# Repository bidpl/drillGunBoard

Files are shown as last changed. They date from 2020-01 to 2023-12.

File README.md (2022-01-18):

# 12V Motor Testing Rig

Code for FRC control board. Manual control FRC motors and air compressor.

We used 12v drills to power 12v FRC motors, (CIMs, BAGs, etc) by removing drill spindle and connecting to motor leads. However, it can not supply large amounts of power. It can not drive Neo motors due to their brushless nature. 

This code is for a meant for a test rig that take a pot input and controls PWM motor controlers (Talon SRXs and Spark Maxes are used in this build).

Features:
Control multiple motors (up to 4) (Control moudes v1.1 and v1.2 have support for 5)
LCD readout for motor power

Documentation is a bit scuffed, I only used the repo while developing the first version (v1.0), didn't for later iterations (v1.1/1.2)

v1.0 was based on an arduino uno with regular potentiometers. The arduino by itself was limited to Talon SRXs since it could not generate a stable enough PWM signal for the Spark Max. This version used regular pin headers and cheap dupont wires so it suffered some durability issues (connections were terrible, shaking the testing rig could disconnect parts).

v1.1/1.2 is uses a custom control module (based on an ATMEGA32P, programs exactly like an UNO) that has an additional PWM driver chip (PCA9685). This chip can generate a proper 50hz PWM signal so it can control Spark Maxes as well. This version also uses locking connectors (JST-XH between input modules and the control module, Molex SL connectors for control module to motor controllers).

## PCB Modules
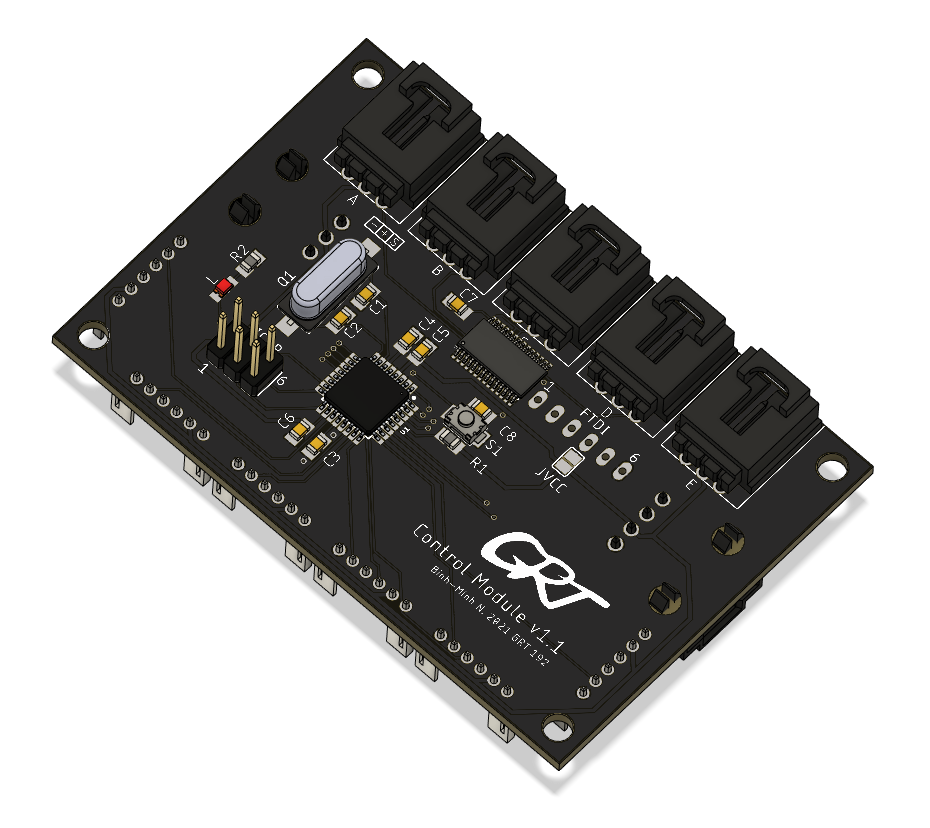
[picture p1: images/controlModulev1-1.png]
Control Module v1.1/v1.2

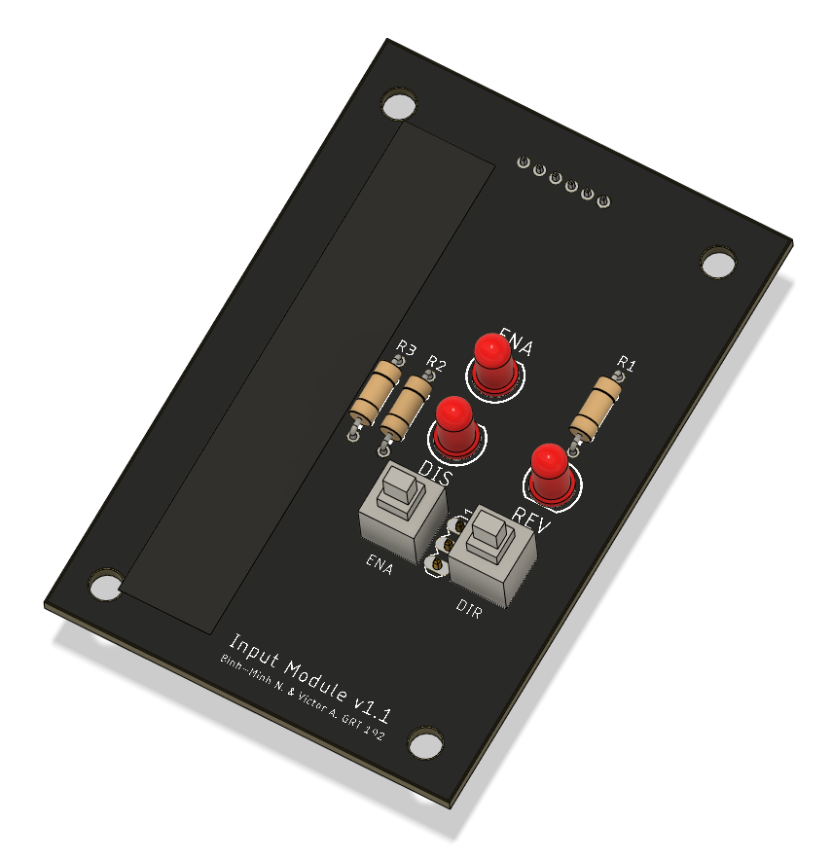
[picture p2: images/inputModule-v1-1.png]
Input Module v1.1


## Testing Rig (The Bomb, name inspired from Die Hard with a Vengeance)
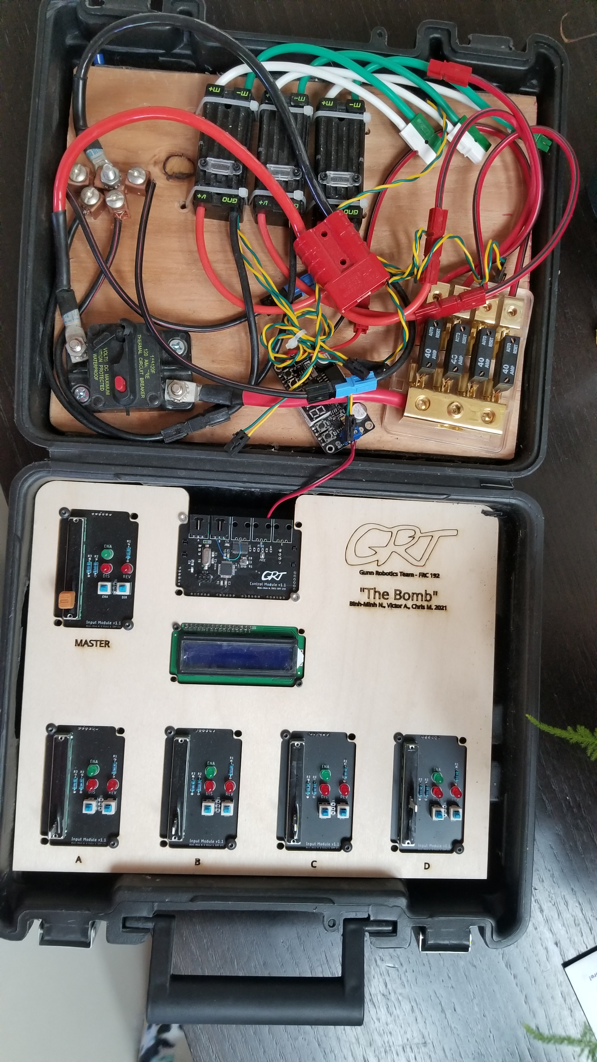
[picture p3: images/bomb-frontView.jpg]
Testing Rig Front View

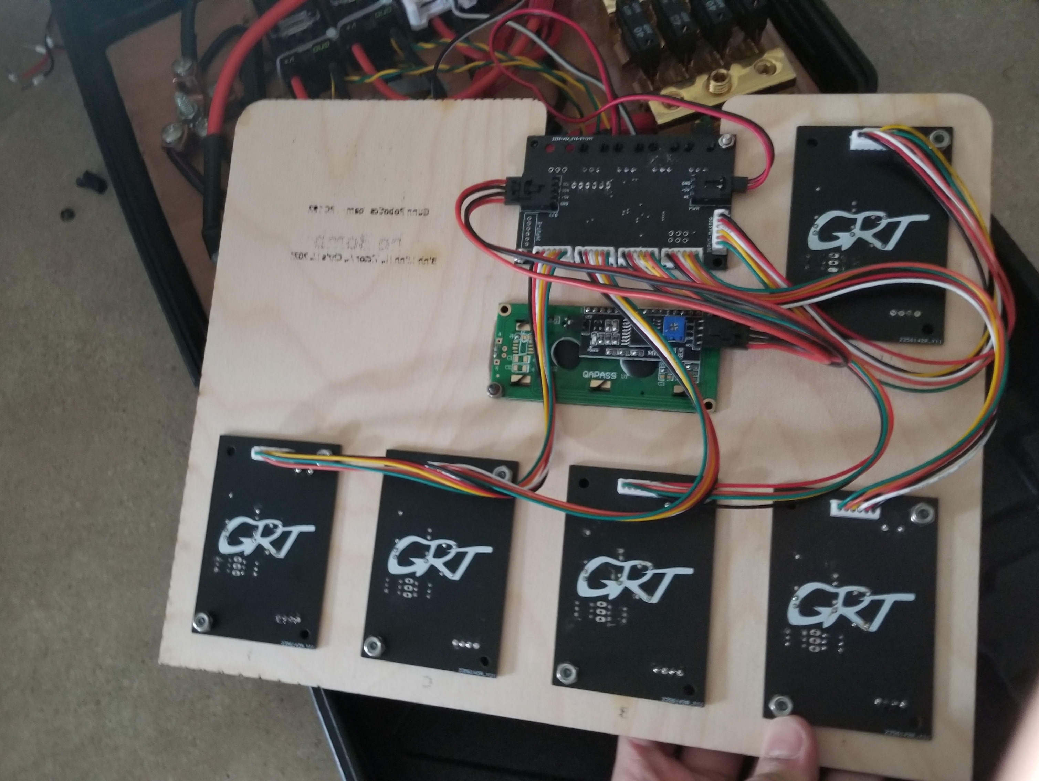
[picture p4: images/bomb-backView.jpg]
Testing Rig Back View


## Change Log
Input Module v1.1:
- Switched from rotate to linear potentiometer
- Switched from horizontal to vertical PCB shape

Control Module v1.2:
- Fixed PCA9685 CE signal (supposed to be active low, was tied high in prev version)

Control Module v1.1:
- Moved from arduino to custom PCB
- Added PCA9685 as PWM signal generator, arduino couldn't get a clean enough PWM signal for some motor controllers (Controlling the LCD delayed the signal too much)
- Switched from loose dupont wire to locking Molex-SL and JST-XH connectors

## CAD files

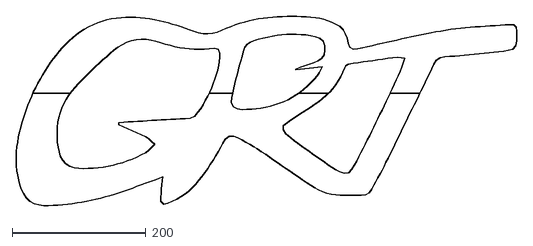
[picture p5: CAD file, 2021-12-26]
pcbs/motorTesting Rig/GRTlogo.dxf
749.8 x 283.4

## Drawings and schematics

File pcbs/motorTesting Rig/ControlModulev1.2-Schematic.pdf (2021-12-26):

# GND VCC 10k

# GND VCC

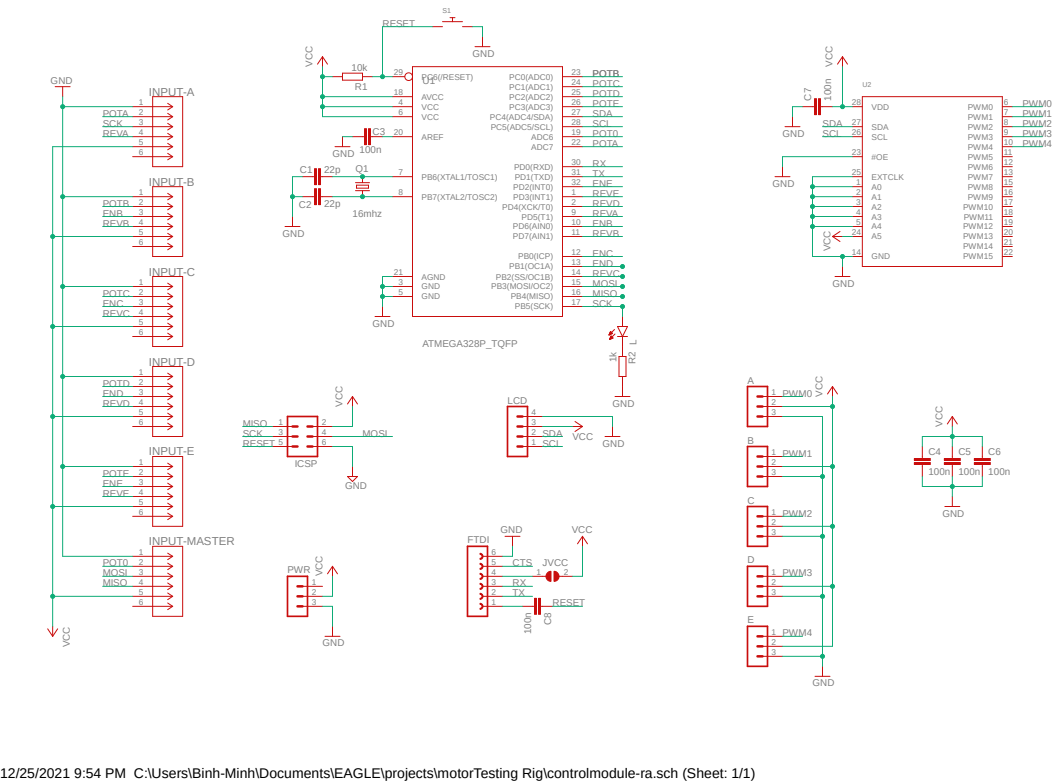
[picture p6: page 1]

12/25/2021 9:54 PM C:\Users\Binh-Minh\Documents\EAGLE\projects\motorTesting Rig\controlmodule-ra.sch (Sheet: 1/1)

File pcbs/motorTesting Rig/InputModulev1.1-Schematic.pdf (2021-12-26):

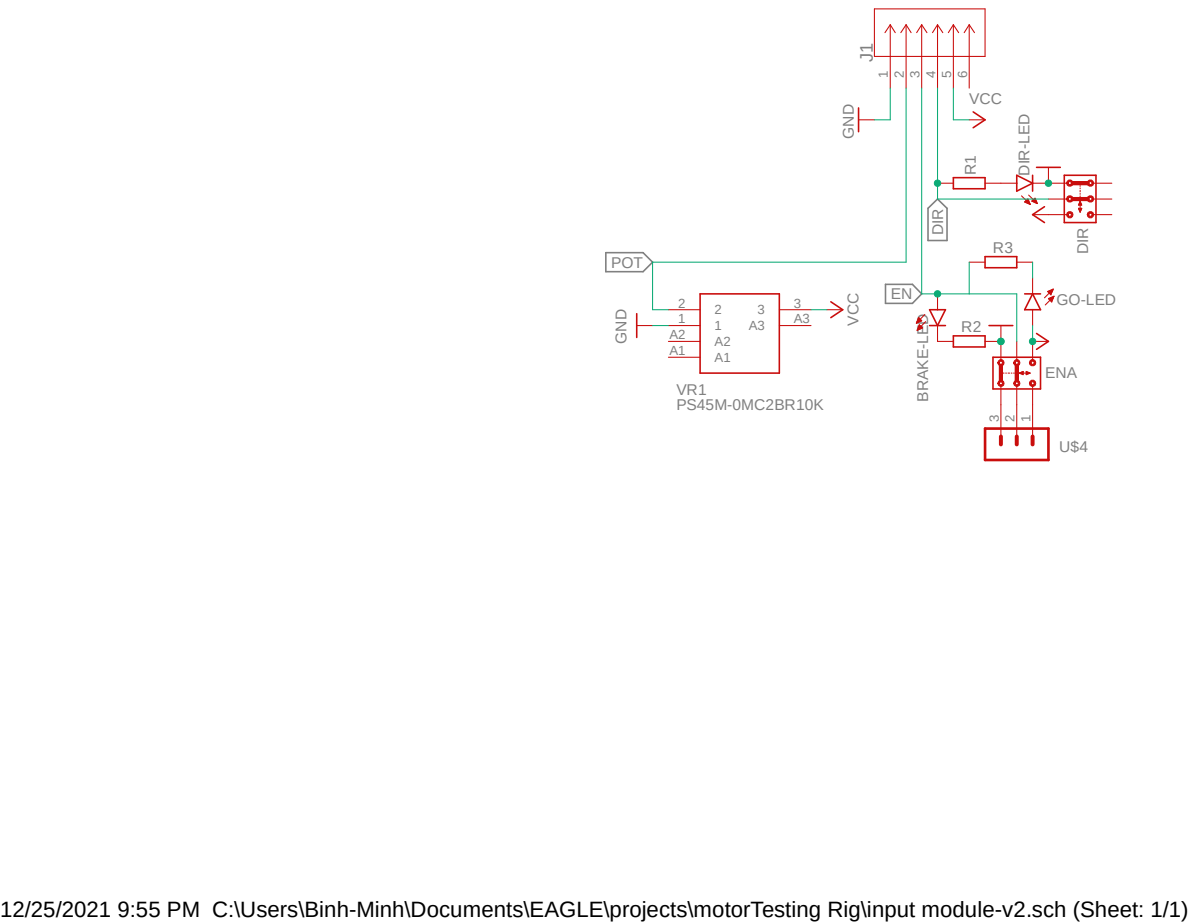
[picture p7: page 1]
12/25/2021 9:55 PM C:\Users\Binh-Minh\Documents\EAGLE\projects\motorTesting Rig\input module-v2.sch (Sheet: 1/1) VCC GND; GND; VCC; ENA DIR BRAKE⁻LED; DIR⁻LED; POT; DIR

GO-LED R¹

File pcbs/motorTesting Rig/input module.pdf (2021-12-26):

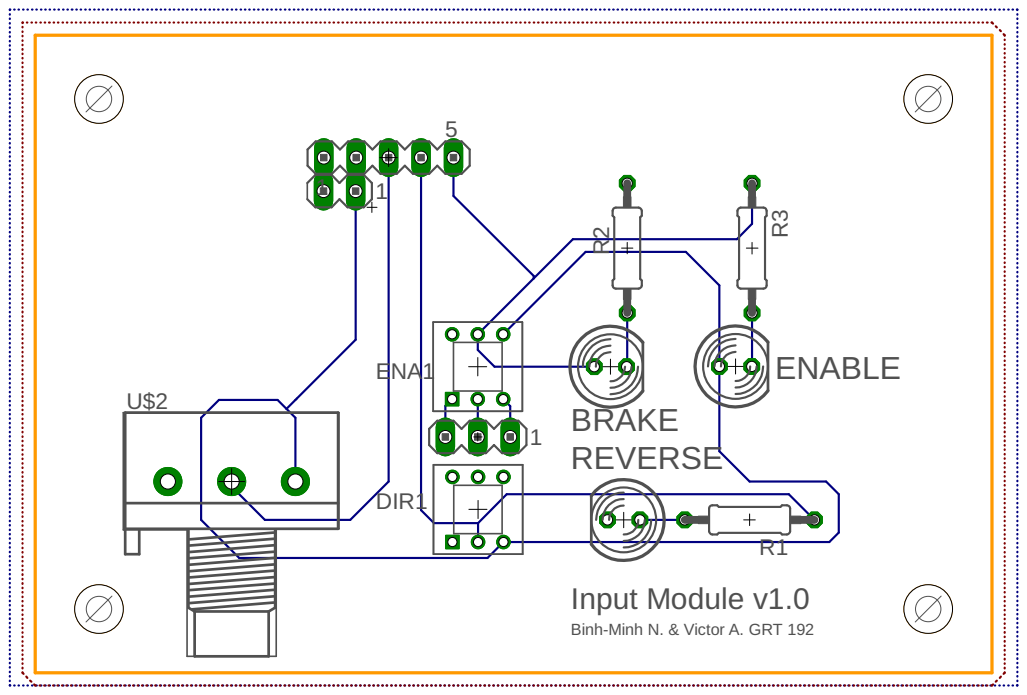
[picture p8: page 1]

Binh-Minh N. & Victor A. GRT 192

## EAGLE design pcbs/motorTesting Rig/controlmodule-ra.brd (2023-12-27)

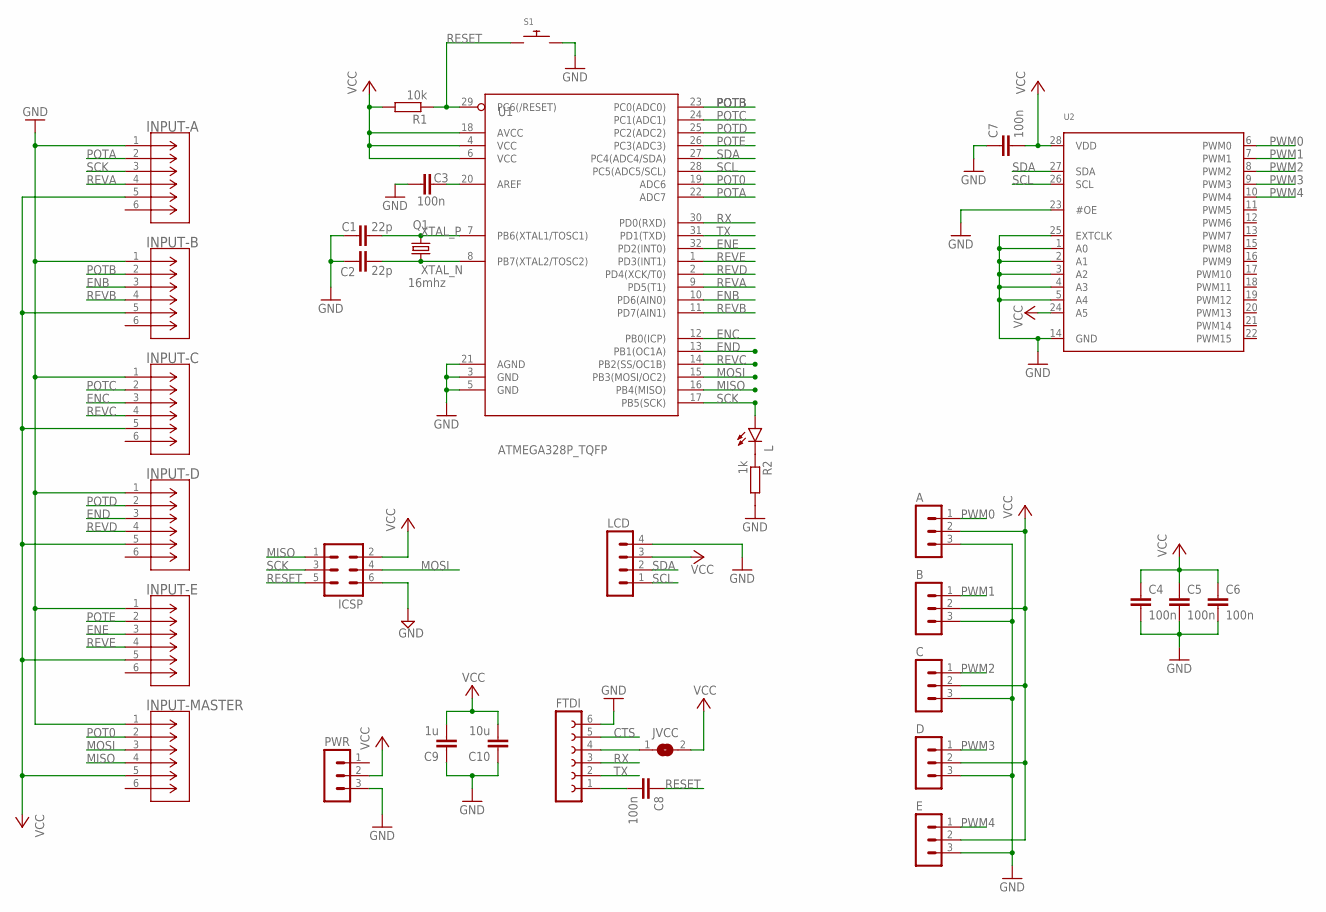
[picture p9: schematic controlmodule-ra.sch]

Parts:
A: MOLEX-SL-3PIN-RA-BOARD-LOCK
B: MOLEX-SL-3PIN-RA-BOARD-LOCK
C: MOLEX-SL-3PIN-RA-BOARD-LOCK
C1, C2: 22p; C0805
C3, C4, C5, C6, C7, C8: 100n; C0805
C9: 1u; C0805
C10: 10u; C0805
D: MOLEX-SL-3PIN-RA-BOARD-LOCK
E: MOLEX-SL-3PIN-RA-BOARD-LOCK
FTDI: FE06-1; FE06
ICSP: MA03-2
INPUT-A: B6B-PH-K-S(LF)(SN)-JST; CONN_B6B-PH-K-S_JST
INPUT-B: B6B-PH-K-S(LF)(SN)-JST; CONN_B6B-PH-K-S_JST
INPUT-C: B6B-PH-K-S(LF)(SN)-JST; CONN_B6B-PH-K-S_JST
INPUT-D: B6B-PH-K-S(LF)(SN)-JST; CONN_B6B-PH-K-S_JST
INPUT-E: B6B-PH-K-S(LF)(SN)-JST; CONN_B6B-PH-K-S_JST
INPUT-MASTER: B6B-PH-K-S(LF)(SN)-JST; CONN_B6B-PH-K-S_JST
JVCC: SJ
L: LEDCHIP-LED0805; CHIP-LED0805
LCD: MOLEX-SL-4PIN-RA-BOARD-LOCK
PWR: MOLEX-SL-3PIN-RA-BOARD-LOCK
Q1: 16mhz; HC49UP
R1: 10k; R0805
R2: 1k; R0805
S1: 3X4MM-PUHSBUTTON; 3X4MM-PUSHBUTTON
U1: ATMEGA328P_TQFP; TQFP32-08
U2: PCA9685; TSSOP28

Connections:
CTS: FTDI.5
ENB: INPUT-B.3, U1.10 (PD6(AIN0))
ENC: INPUT-C.3, U1.12 (PB0(ICP))
END: INPUT-D.3, U1.13 (PB1(OC1A))
ENE: INPUT-E.3, U1.32 (PD2(INT0))
GND: A.3, B.3, C.3, C1.1, C2.1, C3.2, C4.2, C5.2, C6.2, C7.1, C9.1, C10.1, D.3, E.3, FTDI.6, ICSP.6, INPUT-A.1, INPUT-B.1, INPUT-C.1, INPUT-D.1, INPUT-E.1, INPUT-MASTER.1, LCD.4, PWR.3, R2.2, S1.P$2, U1.3 (GND), U1.5 (GND), U1.21 (AGND), U2.1 (A0), U2.2 (A1), U2.3 (A2), U2.4 (A3), U2.5 (A4), U2.14 (GND), U2.23 (#OE), U2.25 (EXTCLK)
MISO: ICSP.1, INPUT-MASTER.4, U1.16 (PB4(MISO))
MOSI: ICSP.4, INPUT-MASTER.3, U1.15 (PB3(MOSI/OC2))
unnamed: FTDI.4, JVCC.1
unnamed: L.C, R2.1
unnamed: C3.1, U1.20 (AREF)
unnamed: C8.2, FTDI.1
POT0: INPUT-MASTER.2, U1.19 (ADC6)
POTA: INPUT-A.2, U1.22 (ADC7)
POTB: INPUT-B.2, U1.23 (PC0(ADC0))
POTC: INPUT-C.2, U1.24 (PC1(ADC1))
POTD: INPUT-D.2, U1.25 (PC2(ADC2))
POTE: INPUT-E.2, U1.26 (PC3(ADC3))
PWM0: A.1, U2.6 (PWM0)
PWM1: B.1, U2.7 (PWM1)
PWM2: C.1, U2.8 (PWM2)
PWM3: D.1, U2.9 (PWM3)
PWM4: E.1, U2.10 (PWM4)
RESET: C8.1, ICSP.5, R1.1, S1.P$1, U1.29 (PC6(/RESET))
REVA: INPUT-A.4, U1.9 (PD5(T1))
REVB: INPUT-B.4, U1.11 (PD7(AIN1))
REVC: INPUT-C.4, U1.14 (PB2(SS/OC1B))
REVD: INPUT-D.4, U1.2 (PD4(XCK/T0))
REVE: INPUT-E.4, U1.1 (PD3(INT1))
RX: FTDI.3, U1.30 (PD0(RXD))
SCK: ICSP.3, INPUT-A.3, L.A, U1.17 (PB5(SCK))
SCL: LCD.1, U1.28 (PC5(ADC5/SCL)), U2.26 (SCL)
SDA: LCD.2, U1.27 (PC4(ADC4/SDA)), U2.27 (SDA)
TX: FTDI.2, U1.31 (PD1(TXD))
VCC: A.2, B.2, C.2, C4.1, C5.1, C6.1, C7.2, C9.2, C10.2, D.2, E.2, ICSP.2, INPUT-A.5, INPUT-B.5, INPUT-C.5, INPUT-D.5, INPUT-E.5, INPUT-MASTER.5, JVCC.2, LCD.3, PWR.2, R1.2, U1.4 (VCC), U1.6 (VCC), U1.18 (AVCC), U2.24 (A5), U2.28 (VDD)
XTAL_N: C2.2, Q1.1, U1.8 (PB7(XTAL2/TOSC2))
XTAL_P: C1.2, Q1.2, U1.7 (PB6(XTAL1/TOSC1))

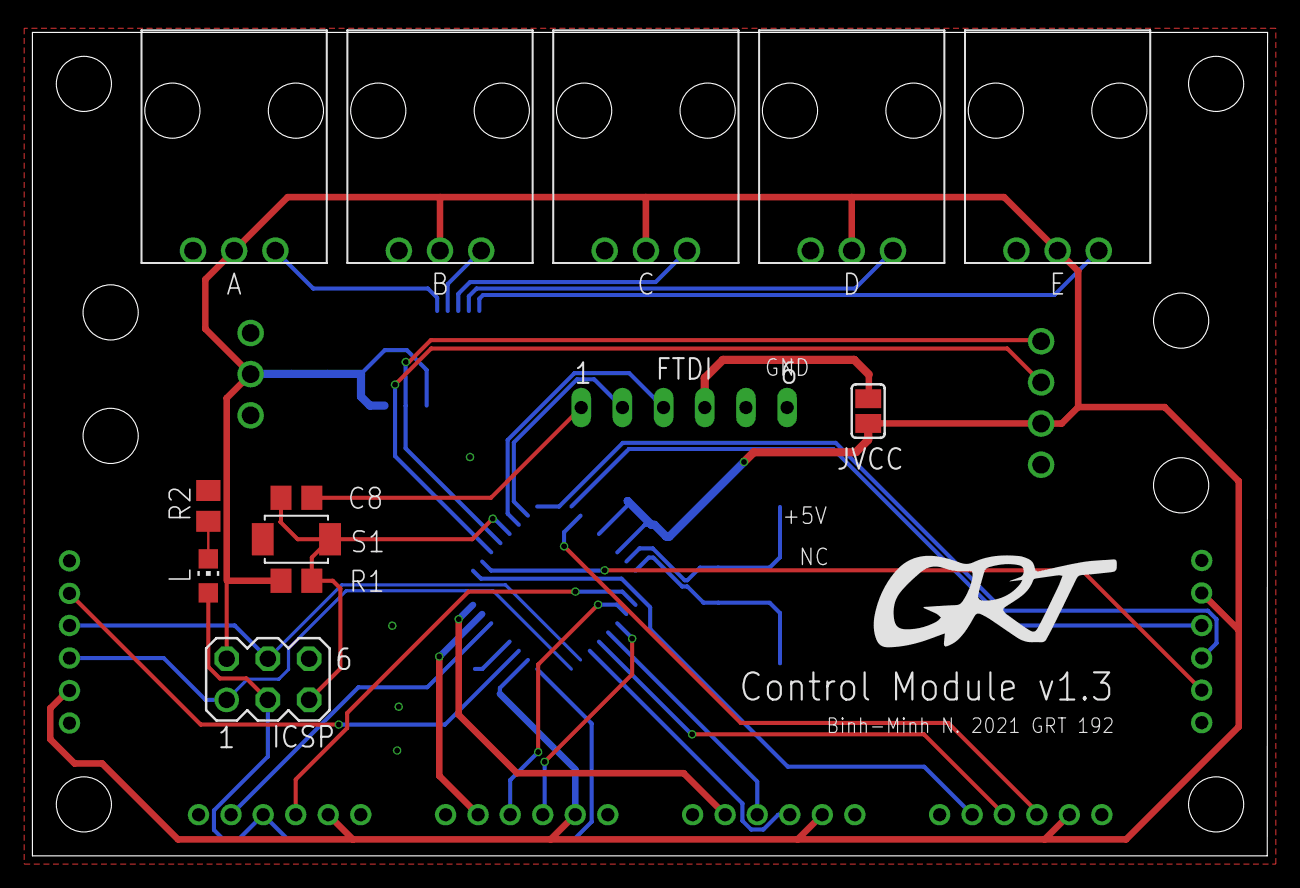
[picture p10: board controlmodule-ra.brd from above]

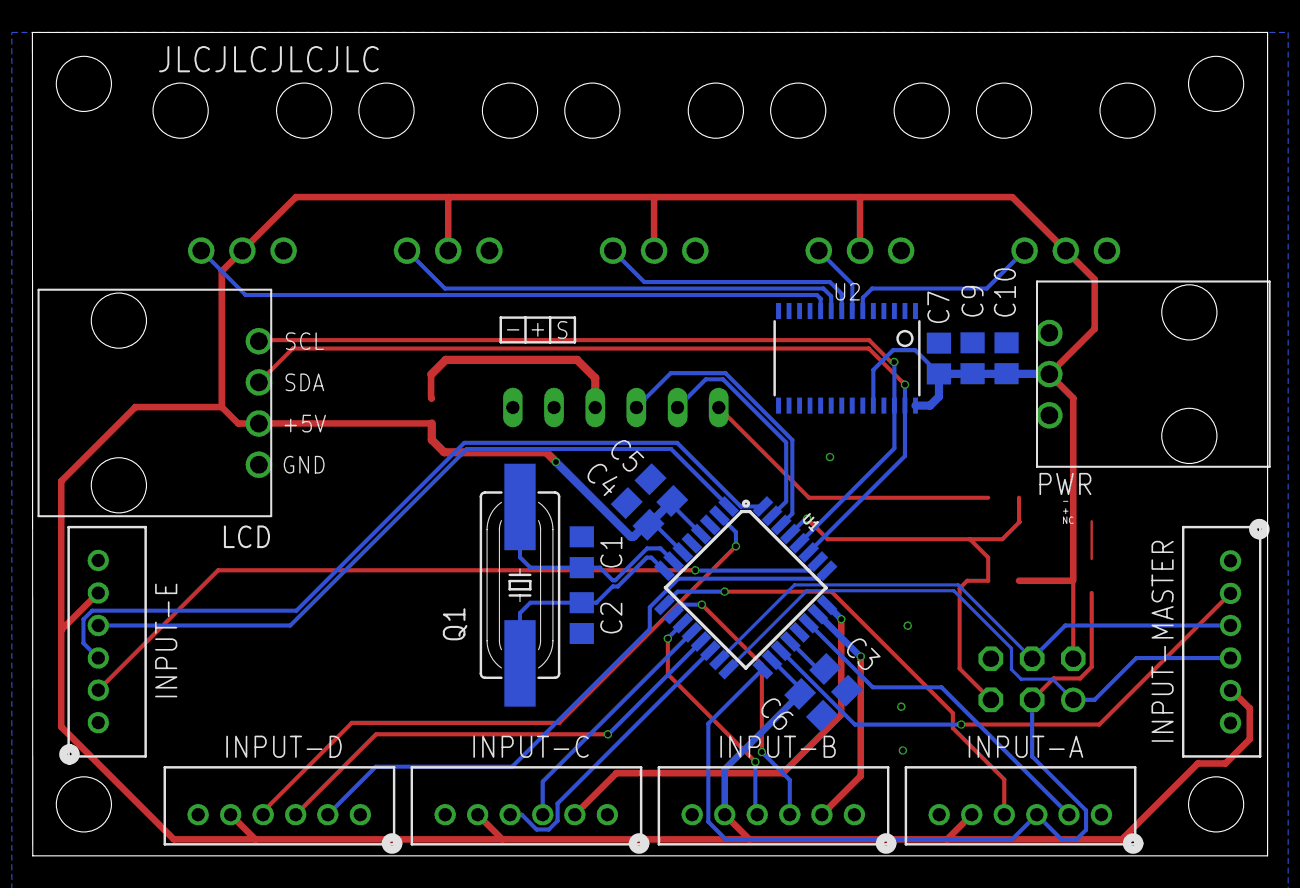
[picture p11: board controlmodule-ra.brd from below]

Board: 2 copper layers, 76.2 x 50.8 mm, 33 parts (20 on the bottom side), 36 nets.

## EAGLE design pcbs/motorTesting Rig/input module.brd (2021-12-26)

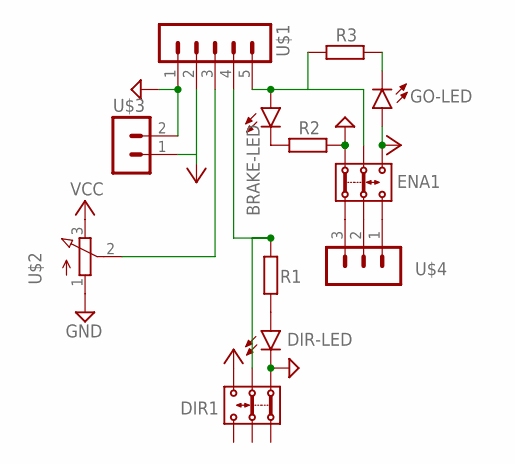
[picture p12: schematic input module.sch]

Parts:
BRAKE-LED: LED5MM
DIR1: DPDT-PUSHBUTTON; 7MM*7MM
DIR-LED: LED5MM
ENA1: DPDT-PUSHBUTTON; 7MM*7MM
GO-LED: LED5MM
R1, R2, R3: R-EU_0207/10; 0207/10
U$1: MALE-HEADER-5PIN; MA05-1
U$2: POTENTIOMETER-16MM; 3RP/1610N
U$3: MALE-HEADER-2PIN; MA02-1
U$4: MALE-HEADER-3PIN; MA03-1

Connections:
GND: DIR1.1, DIR-LED.K (C), ENA1.6, R2.2, U$1.1, U$2.1 (A), U$3.2 (3)
unnamed: U$1.3, U$2.2 (S)
unnamed: BRAKE-LED.A, ENA1.5, R3.1, U$1.5
unnamed: DIR1.2, R1.1, U$1.4
unnamed: DIR-LED.A, R1.2
unnamed: ENA1.3, U$4.1
unnamed: ENA1.2, U$4.2
unnamed: ENA1.1, U$4.3
unnamed: BRAKE-LED.K (C), R2.1
unnamed: GO-LED.K (C), R3.2
VCC: DIR1.3, ENA1.4, GO-LED.A, U$1.2, U$2.3 (E), U$3.1 (2)

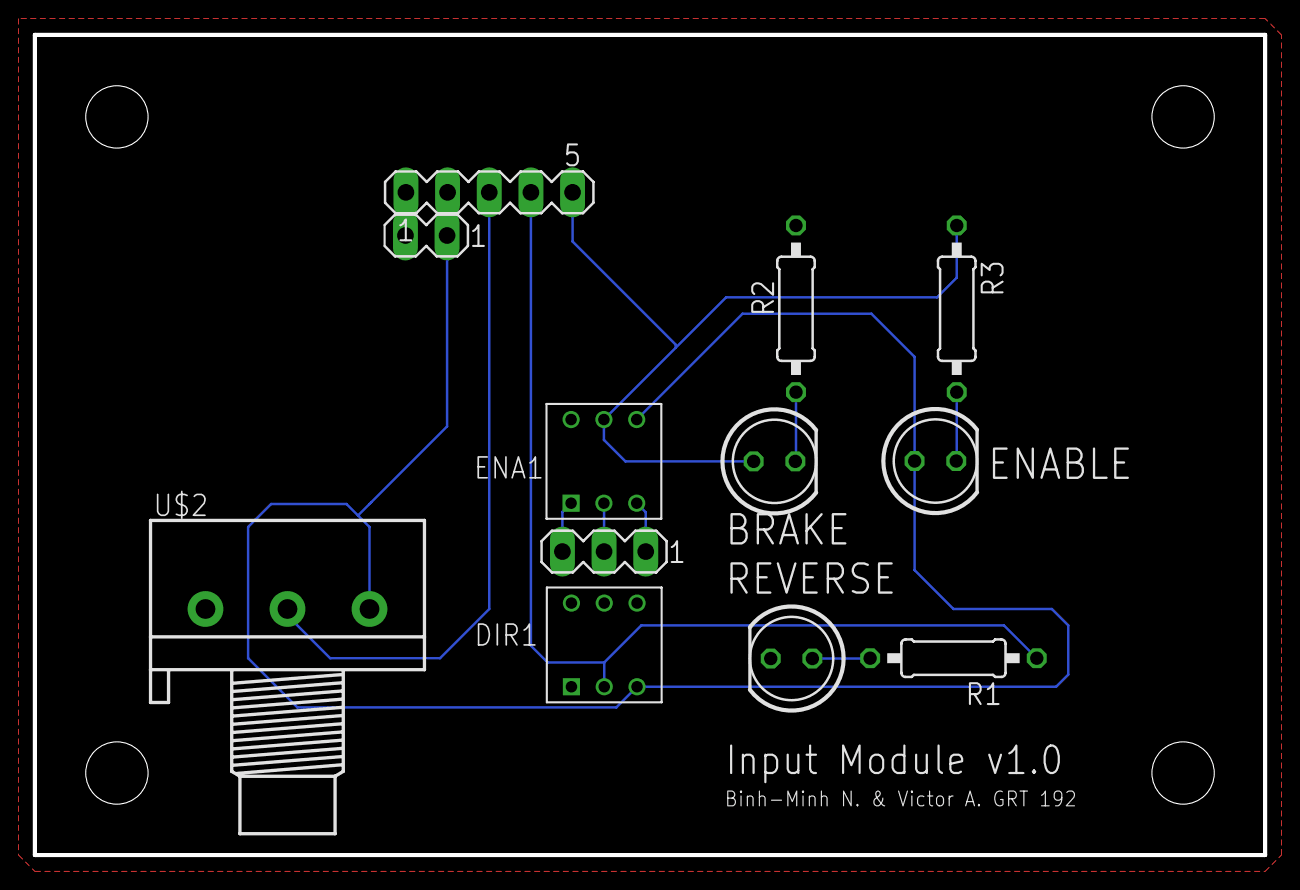
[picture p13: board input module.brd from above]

Board: 2 copper layers, 75.0 x 50.0 mm, 12 parts (0 on the bottom side), 11 nets.

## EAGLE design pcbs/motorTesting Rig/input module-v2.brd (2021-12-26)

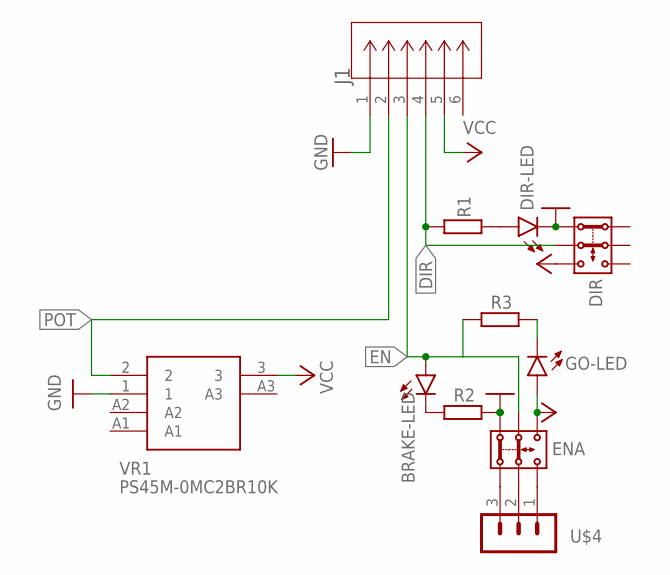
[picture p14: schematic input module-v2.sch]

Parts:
BRAKE-LED: LED5MM
DIR: DPDT-PUSHBUTTON; 7MM*7MM
DIR-LED: LED5MM
ENA: DPDT-PUSHBUTTON; 7MM*7MM
GO-LED: LED5MM
J1: B6B-PH-K-S(LF)(SN)-JST; CONN_B6B-PH-K-S_JST
R1, R2, R3: R-EU_0207/10; 0207/10
U$4: MALE-HEADER-3PIN; MA03-1
VR1: PS45M-0MC2BR10K; PS45M0MC2BR10K

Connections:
DIR: DIR.2, J1.4, R1.1
EN: BRAKE-LED.A, ENA.5, J1.3, R3.1
GND: DIR.1, DIR-LED.K (C), ENA.6, J1.1, R2.2, VR1.1
unnamed: DIR-LED.A, R1.2
unnamed: ENA.3, U$4.1
unnamed: ENA.2, U$4.2
unnamed: ENA.1, U$4.3
unnamed: BRAKE-LED.K (C), R2.1
unnamed: GO-LED.K (C), R3.2
POT: J1.2, VR1.2
VCC: DIR.3, ENA.4, GO-LED.A, J1.5, VR1.3

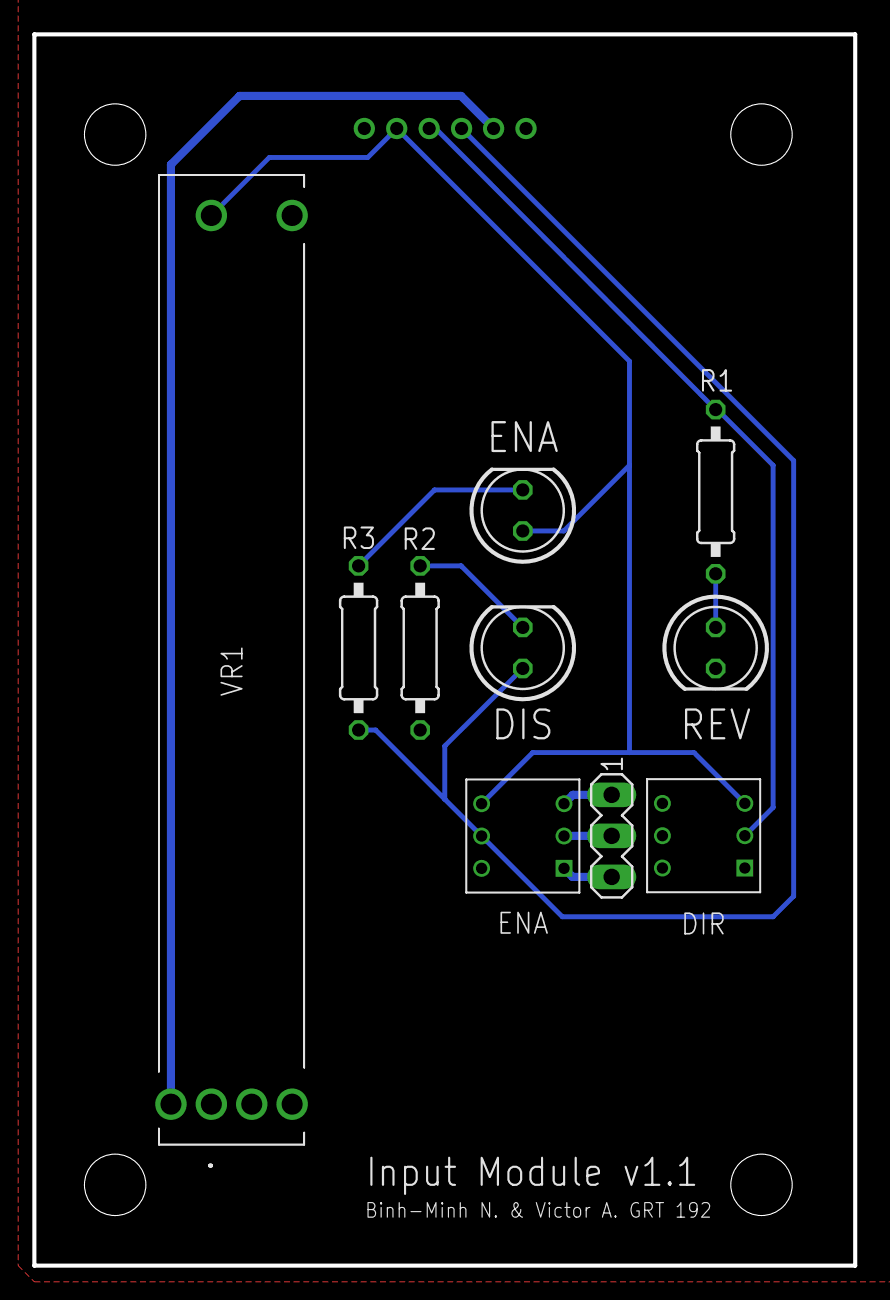
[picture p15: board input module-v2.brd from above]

Board: 2 copper layers, 50.8 x 76.2 mm, 11 parts (1 on the bottom side), 11 nets.

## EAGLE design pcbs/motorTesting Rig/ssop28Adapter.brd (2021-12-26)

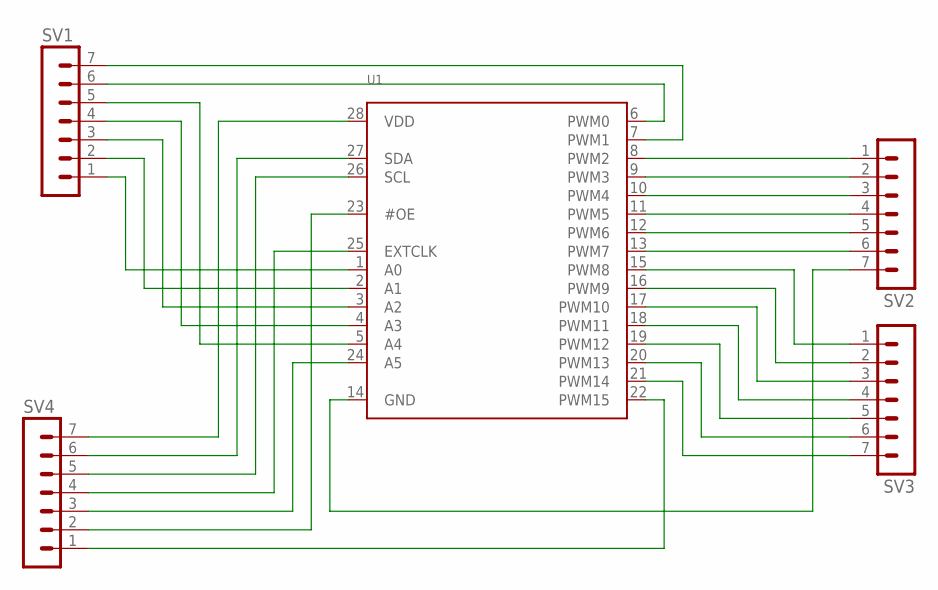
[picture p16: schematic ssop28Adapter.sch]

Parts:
SV1, SV2, SV3, SV4: MA07-1
U1: PCA9685; TSSOP28

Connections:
unnamed: SV1.1, U1.1 (A0)
unnamed: SV1.2, U1.2 (A1)
unnamed: SV1.3, U1.3 (A2)
unnamed: SV1.4, U1.4 (A3)
unnamed: SV1.5, U1.5 (A4)
unnamed: SV1.6, U1.6 (PWM0)
unnamed: SV1.7, U1.7 (PWM1)
unnamed: SV2.1, U1.8 (PWM2)
unnamed: SV2.2, U1.9 (PWM3)
unnamed: SV2.3, U1.10 (PWM4)
unnamed: SV2.4, U1.11 (PWM5)
unnamed: SV2.5, U1.12 (PWM6)
unnamed: SV2.6, U1.13 (PWM7)
unnamed: SV2.7, U1.14 (GND)
unnamed: SV3.1, U1.15 (PWM8)
unnamed: SV3.2, U1.16 (PWM9)
unnamed: SV3.3, U1.17 (PWM10)
unnamed: SV3.4, U1.18 (PWM11)
unnamed: SV3.5, U1.19 (PWM12)
unnamed: SV3.6, U1.20 (PWM13)
unnamed: SV3.7, U1.21 (PWM14)
unnamed: SV4.1, U1.22 (PWM15)
unnamed: SV4.2, U1.23 (#OE)
unnamed: SV4.3, U1.24 (A5)
unnamed: SV4.4, U1.25 (EXTCLK)
unnamed: SV4.5, U1.26 (SCL)
unnamed: SV4.6, U1.27 (SDA)
unnamed: SV4.7, U1.28 (VDD)

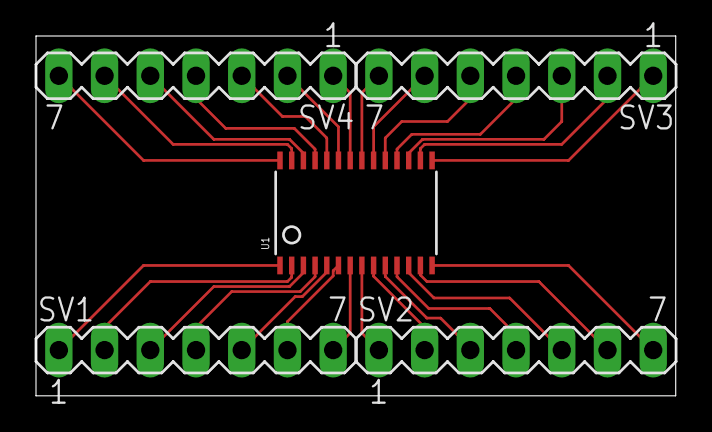
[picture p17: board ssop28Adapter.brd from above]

Board: 2 copper layers, 35.5 x 20.0 mm, 5 parts (0 on the bottom side), 28 nets.

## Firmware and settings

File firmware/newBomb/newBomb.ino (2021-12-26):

/* Firmware for "The Bomb" (GRT - FRC 192)
 * Made in 2020-21
 * 
 * Binh-Minh Nguyen
 * binhminh292@gmail.com 
 * 
 * I'm commenting this like a year later sorry if it's unclear
 * 
 * Control board (PCB) supports 5 inputs + 1 master, code currently has 4 inputs + 1 master
 * 
 * pot = slider pin
 * en = enable pin
 * rev = reverse pin
 */

#include <Wire.h>
#include <hd44780.h>                       // main hd44780 header
#include <hd44780ioClass/hd44780_I2Cexp.h> // i2c expander i/o class header

hd44780_I2Cexp lcd; // declare lcd object: auto locate & auto config expander chip

// LCD geometry
const int LCD_COLS = 16;
const int LCD_ROWS = 2;

// pattern for the disable character (circle with x)
byte disableChar[] = {
  0b00000,
  0b01110,
  0b10101,
  0b11011,
  0b10101,
  0b01110,
  0b00000,
  0x00
};


//Declare input pins
//Includes master input, master is stored as first value in each array
//I really should have created an inputModule class, but I'm lazy
#define numInputs 5

byte pot[] = {A6, A7, A0, A1, A2};
byte en[] = {11, 13, 6, 8, 9};
byte rev[] = {12, 5, 7, 10, 4};

int potData[numInputs];
int enData[numInputs];
int revData[numInputs];

//Positions for A,B,C, and D outputs on the LCD
int displayOffset[][2] = {{0,0},{8,0},{0,1},{8,1}};

//Scaled output for each channel
long percentOutput[numInputs];

void setup() {
  // Begin Serial connection w/ computer if connected
  Serial.begin(9600);

  //Initialize LCD
  int status;

  status = lcd.begin(LCD_COLS, LCD_ROWS);
  if(status) // non zero status means it was unsuccesful
  {
    // hd44780 has a fatalError() routine that blinks an led if possible
    // begin() failed so blink error code using the onboard LED if possible
    hd44780::fatalError(status); // does not return
  }

  // Save disable character to slot 0
  lcd.createChar(0, disableChar);

  //initialize PCA9685 driver IC (I2C to PWM chip), see datasheet for what these registers are
  //Enable sleep mode to change PRE_SCALE (determines pwm frequency)
  writeRegister(0x60, 0x00, 0x11);
  //Change PRE_SCALE to 7Dh (20ms period/50hz frequency)
  writeRegister(0x60, 0xFE, 0x7B);
  //Disable sleep mode/turn the internal osciallator on
  writeRegister(0x60, 0x00, 0x01);

  // Initialize input pins
  for(int i = 0; i < numInputs; i++){
    pinMode(pot[i], INPUT);
    pinMode(en[i], INPUT);
    pinMode(rev[i], INPUT);
  }

  // Print the channel names to the LCD
  lcd.clear();
  lcd.setCursor(displayOffset[0][0], displayOffset[0][1]);
  lcd.write("A:");
  lcd.setCursor(displayOffset[1][0], displayOffset[1][1]);
  lcd.write("B:");
  lcd.setCursor(displayOffset[2][0], displayOffset[2][1]);
  lcd.write("C:");
  lcd.setCursor(displayOffset[3][0], displayOffset[3][1]);
  lcd.write("D:");
}

void loop() {
  //Updates input values (get slider and button positions)
  for(int i = 0; i < numInputs; i++){
    potData[i] = analogRead(pot[i]);
    enData[i] = digitalRead(en[i]);
    revData[i] = digitalRead(rev[i]);

    //Old Debugging prints
//    Serial.print(potData[i]);
//    Serial.print(" ");
//    Serial.print(enData[i]);
//    Serial.print(" ");
//    Serial.println(revData[i]);
  }

  
  for(byte i = 1; i < numInputs; i++){
    lcd.setCursor(displayOffset[i-1][0] + 2, displayOffset[i-1][1]);
    
    //EN active Low
    if(enData[i] == HIGH){
      //write disable symbol
      lcd.write(0);
    }else{
      //Clear disable symbol
      lcd.write(" ");
    }

    //If under master control, read master potentiometer, else read normal potentiometer
    if(enData[0] == LOW){
      //Deadband at 1021 (Assume 1021 or higher is full ouput)
      percentOutput[i] = (potData[0] > 1015) ? 100 : (long) potData[0] * 100 / 1023;

      revData[i] = revData[i] ^ revData[0];
      Serial.print("master: ");
    }else{
      //Deadband at 1021 (Assume 1021 or higher is full ouput)
      percentOutput[i] = (potData[i] > 1015) ? 100 : (long) potData[i] * 100 / 1023;
      Serial.print("Regular: ");
    }

    
    //REV active HIGH
    if(revData[i] == HIGH){
      lcd.write("-");
    }else{
      lcd.write(" ");
    }

    //Pad whitespace for 1 and 2 digit numbers
    if(percentOutput[i] < 100){
      lcd.print(" ");
      if(percentOutput[i] < 10){
        lcd.print(" ");
      }
    }

    //Update percentOutput based on enable signal and slider position
    if(enData[i] == LOW){
      setPower(i-1, (int) percentOutput[i] * (revData[i] ? -1 : 1));
      Serial.print(" ");
    }else{
      setPower(i-1, 0);
    }
    lcd.print(String((int) percentOutput[i]));
    Serial.println(String((int) percentOutput[i]));
  }

  Serial.println();
//  delay(500);
}

//Unused method, was only used to figure out communication with the PCA9685 chip
byte readRegister(byte devAddr, byte regAddr){  
  Wire.beginTransmission(devAddr);
  Wire.write(regAddr);              // sends one byte
  Wire.endTransmission();    // stop transmitting


  Wire.requestFrom(devAddr, 1);
  byte data = Wire.read();
  return data;
}

//Unused method, was only used to figure out communication with the PCA9685 chip
void printRegister(byte devAddr, byte regAddr){
  Serial.print(devAddr, HEX);
  Serial.print(" ");
  Serial.print(regAddr, HEX);
  Serial.print(": ");
  Serial.println(readRegister(devAddr, regAddr), HEX);
}

// Tells PCA9685 at I2C address devAddr to write data to its register at address regAddr (see datasheet)
byte writeRegister(byte devAddr, byte regAddr, byte data){
  Wire.beginTransmission(devAddr);
  Wire.write(regAddr);
  Wire.write(data);
  Wire.endTransmission();
}

// Tells PCA9685 to set a channel's output
// See schematic to see which channel (letter) corresponds to which channel (pin #) 
// Basically go read the datasheet to understand what this is doing
void setPower(byte channel, int percentOutput){
  // Scales percentOutput [-100 to 100] to PCA9685's counter
  int output = 0x133 + 0x67 * percentOutput/100;
  
  //Set on time to 0
  writeRegister(0x60, 0x06 + 4*channel, 0);
  writeRegister(0x60, 0x07 + 4*channel, 0);
  //Set off time to 133h (307d) 1.5 ms pulse width
  writeRegister(0x60, 0x08 + 4*channel, output & 0xff);
  writeRegister(0x60, 0x09 + 4*channel, (output >> 8) & 0xff);

  Serial.println(output & 0xff, HEX);
  Serial.println((output >> 8) & 0xff, HEX);
}

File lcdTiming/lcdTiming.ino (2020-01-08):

#include <LiquidCrystal_I2C.h>
#include <Wire.h>

#define talon1 6
#define talon2 9
#define talon3 10
#define talon4 11

#define dir1 0
#define dir2 2
#define dir3 4
#define dir4 7

#define ena1 1
#define ena2 3
#define ena3 5
#define ena4 8

#define pot1 A0
#define pot2 A1
#define pot3 A2
#define pot4 A3

#define dirMaster 12
#define enaMaster 13

int a;
int b;
int c;
int d;

int master;

double aPower;
double bPower;
double cPower;
double dPower;

double masterPower;

int aDelay;
int bDelay;
int cDelay;
int dDelay;

byte disableChar[] = {
  B00000,
  B01110,
  B10101,
  B11011,
  B10101,
  B01110,
  B00000,
};

LiquidCrystal_I2C lcd(0x27, 16, 2); // set the LCD address to 0x27 for a 16 chars and 2 line display

unsigned long time1;

void setup() {
  // put your setup code here, to run once:
  //Serial.begin(9600);

  pinMode(talon1, OUTPUT);
  pinMode(talon2, OUTPUT);
  pinMode(talon3, OUTPUT);
  pinMode(talon4, OUTPUT);

  pinMode(dir1, INPUT);
  pinMode(dir2, INPUT);
  pinMode(dir3, INPUT);
  pinMode(dir4, INPUT);

  pinMode(ena1, INPUT);
  pinMode(ena2, INPUT);
  pinMode(ena3, INPUT);
  pinMode(ena4, INPUT);

  pinMode(dirMaster, INPUT);
  pinMode(enaMaster, INPUT);

  lcd.init();
  lcd.backlight();

  lcd.createChar(0, disableChar);
  
  lcd.setCursor(0, 0);
  lcd.print("A: ");
  lcd.setCursor(8, 0);
  lcd.print("C: ");
  lcd.setCursor(0, 1);
  lcd.print("B: ");
  lcd.setCursor(8, 1);
  lcd.print("D: ");
}

void loop() {
  //Serial.println(digitalRead(enaMaster));
  
  if(digitalRead(enaMaster) == 0){
    //Makes value negative if dir pin triggered
    master = readPot(pot1) * -1 * (digitalRead(dirMaster)*2-1);

    aPower = toPower(master, digitalRead(dir1));
    bPower = toPower(master, digitalRead(dir2));
    cPower = toPower(master, digitalRead(dir3));
    dPower = toPower(master, digitalRead(dir4));
  }else{
    a = readPot(pot1);
    b = readPot(pot2);
    c = readPot(pot3);
    d = readPot(pot4);
  
    aPower = toPower(a, digitalRead(dir1));
    bPower = toPower(b, digitalRead(dir2));
    cPower = toPower(c, digitalRead(dir3));
    dPower = toPower(d, digitalRead(dir4));
  }
    
  printPower(3, 0, aPower, digitalRead(ena1));
  printPower(3, 1, bPower, digitalRead(ena2));
  printPower(11, 0, cPower, digitalRead(ena3));
  printPower(11, 1, dPower, digitalRead(ena4));

  aPower = (digitalRead(ena1) == 0) ? aPower : 0;
  bPower = (digitalRead(ena2) == 0) ? bPower : 0;
  cPower = (digitalRead(ena3) == 0) ? cPower : 0;
  dPower = (digitalRead(ena4) == 0) ? dPower : 0;

  aDelay = 1490 + aPower*500;
  bDelay = 1490 + bPower*500;
  cDelay = 1490 + cPower*500;
  dDelay = 1490 + dPower*500;

  
  pwmPulse(talon1, aDelay);
  pwmPulse(talon2, bDelay);
  pwmPulse(talon3, cDelay);
  pwmPulse(talon4, dDelay);
}

void printPower(int x, int y, double power, int ena){
  lcd.setCursor(x - 1,y);

  if(ena == 0){
    lcd.print(" ");
  }else{
    lcd.write(0);
  }
  
  if(power >= 0){
    lcd.print(" ");
  }
  lcd.print(power);
}

void pwmPulse(unsigned int pin, int time1){
  digitalWrite(pin, HIGH);
  delayMicroseconds(time1);
  digitalWrite(pin, LOW);
}

int readPot(int pin){
  analogRead(pin);
  return analogRead(pin);
}

double toPower(int sensorVal, int forward){
    return ((double)sensorVal) / 1023 * (forward*2-1) * -1.0;
}

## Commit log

2019-05-07 Updated READEME.md, created arduino project file. Added code for LCD control and Joystick input
2019-07-14 now drives PWM motor controller and potentiometer support
2020-01-08 Redid stuff, now works with the Not Bomb tm. Use lcdTiming.ino, B and C are switched from physical order
2021-12-26 Added EAGLE files, line endings might be a bit messed up in that folder
    [GRTlogo.dxf, controlmodule-ra-12.brd, controlmodule-ra-12.sch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]
2023-12-27 control board v1.3, moved stuff to bottom side to avoid aluminum shavings
    [controlmodule-ra-12.brd, controlmodule-ra-12.sch, controlmodule-ra.brd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]

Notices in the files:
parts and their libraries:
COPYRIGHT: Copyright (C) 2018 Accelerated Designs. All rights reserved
